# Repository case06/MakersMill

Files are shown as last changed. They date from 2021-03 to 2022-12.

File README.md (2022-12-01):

# MakersMill

[](
    https://opensourceecology.de)

This is the source repo for the "Maker's Mill"-Projekt on

https://wiki.opensourceecology.de/Maker%27s_Mill

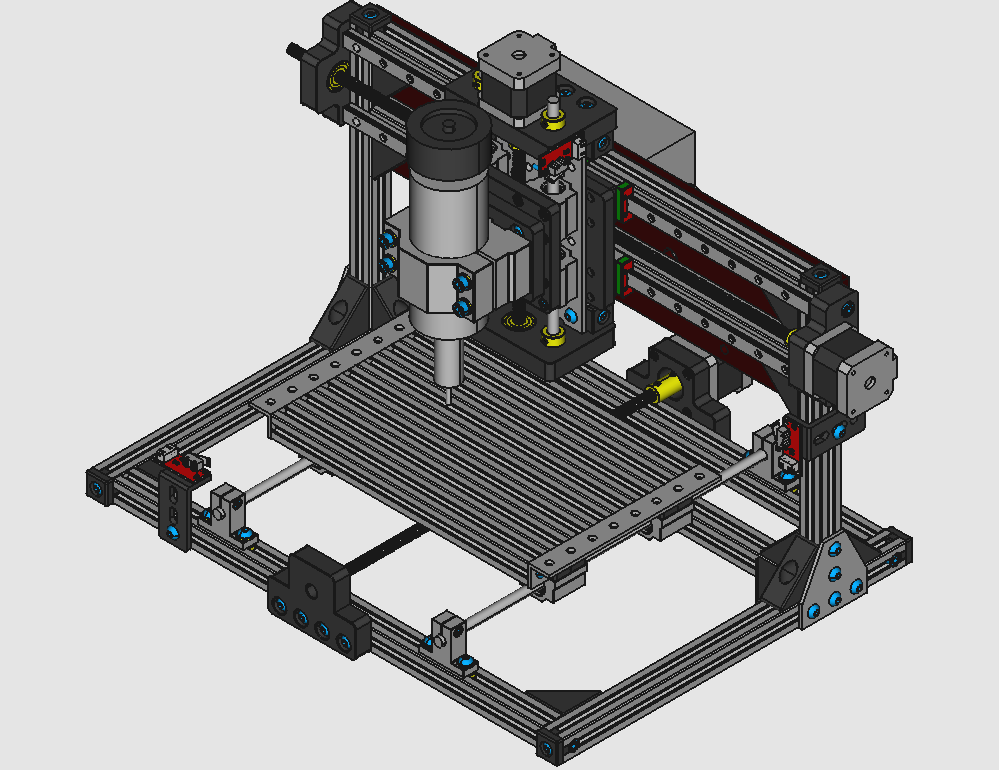
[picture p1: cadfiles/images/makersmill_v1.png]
Maker's Mill V.1.0
<p></p>

The projekt is based on the UniProKit 3D-part-library UPKlib V2.06, which is available at 

<a href="https://github.com/case06/upklib_v2"> https://github.com/case06/upklib_v2 </a>

The FreeCAD-sourcefiles of the current version can be viewed or modified with FreeCAD version 18 and 19

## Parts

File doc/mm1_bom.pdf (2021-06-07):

Seite 1

BOM Maker's Mill MM1 Desktop-Fräse V1.02, UniProKit UPKlib V2.06

Partname | PartNo. | Quantity Description | Pos | Supplier

Basis-Set
Tslot32con | 17092218 | 2 | T-Slot Con, 320x20x20mm | 1 | ML
Tslot40 | 17092208 | 5 | T-Slot Nut 6, 400x20x20mm | 2 | ML
Tslot24con | 17092217 | 2 | T-Slot Con, 240x20x20mm | 3 | ML
Tslot24 | 17092206 | 8 | T-Slot Nut 6, 240x20x20mm | 4 | ML
Tslot8 | 17092203 | 2 | T-Slot Nut 6, 80x20x20mm | 5 | ML
Flat16 | 17092239 | 2 | Flach, 160x40x4mm | 6 | ML
Angle16 | 17092228 | 2 | L-Profil, 160x20x20mm | 7 | ML
TCon | 17092302 | 2 | Flach, 60x60x4mm | 8 | ML
RAconnector | 17092313 | 18 | 90° Versteifungswinkel | 9 | ML
EndCap1d | 17092315 | 14 | Endkappe | 10 | ML
M6nutplate | 17092309 | 104 | für TSlot, Slot6, M6 | 11 | ML
M6x25cyl | 17092307 | 6 | 25mm, M6 DIN 7984 | 12 | ML, SP
M6x16 | 17092305 | 21 | 16mm, M6 ISO 7380 | 13 | ML, SP
M6x12 | 17092304 | 68 | 12mm, M6 ISO 7380 | 14 | ML, SP
M6x8 | 17092303 | 55 | 8mm, M6 ISO 7380 | 15 | ML, SP
M6wash | 17092310 | 12 | 6.4x12x1.6, DIN 125 | 16 | ML, SP
M6nut | 17092308 | 12 | 5.6x10mm, M6 DIN934 | 17 | ML, SP

Box-Set
3.5x16ws | 18081701 | 4 | WoodScrew | 18 | ML, SP

Set Lineardrive 1
M4nut | 19070613 | 12 | M4 Nut | 19 | ML, SP
M3x10cyl | 19070615 | 6 | 10mm, M3 ISO 4762 | 20 | ML, SP

Set Lineardrive 2
Mountplate3d | 21040802 | 1 | Motorplatte links | 21 | ML
Endplate1b | 19070624 | 0 | Loslager-Platte | 22 | ML
608ZZ_Ball_Bearing | 19082001 | 3 | Kugellager, 8mm innen | 23 | ML, SP
Carriageplate | 19070624 | 1 | Schlittenplatte | 24 | ML

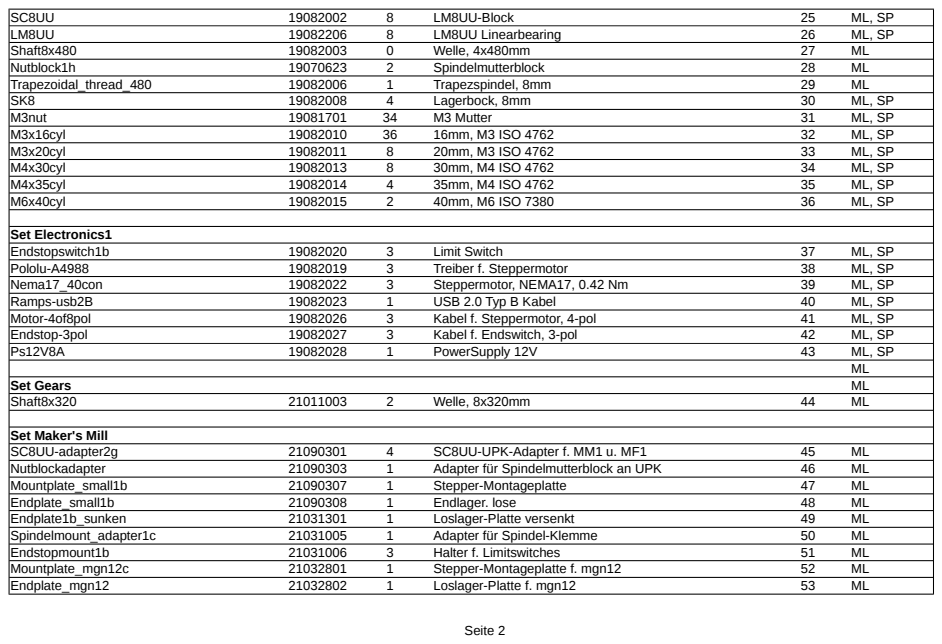
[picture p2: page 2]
Seite; LM8UU-Block; LM8UU Linearbearing; Shaft8x480; Welle, 4x480mm; Nutblock1h; Spindelmutterblock; Trapezoidal_thread_480; Trapezspindel, 8mm; Lagerbock, 8mm; M3nut; M3 Mutter; M3x16cyl; 16mm, M3 ISO 4762; M3x20cyl; 20mm, M3 ISO 4762; M4x30cyl; 30mm, M4 ISO 4762; M4x35cyl; 35mm, M4 ISO 4762; M6x40cyl; 40mm, M6 ISO 7380; Set Electronics1; Endstopswitch1b; Limit Switch; Pololu-A4988; Treiber f. Steppermotor; Nema17_40con; Steppermotor, NEMA17, 0.42 Nm; Ramps-usb2B; USB 2.0 Typ B Kabel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

Set Maker's Mill

Seite

3

Carriageplate-mgn12b | 21032810 | 1 | Schlittenplatte f. MGN12 | 54 | ML
M4x10cyl | 21090302 | 32 | 10mm, M4 ISO 4762 | 55 | ML, SP
M4x4lockscrew | 21090310 | 12 | M4x4 Madenschraube | 56 | ML, SP
M6x65cyl | 21031002 | 4 | 65mm, M6 ISO 7380 | 57 | ML, SP
M3x30cyl | 21032809 | 4 | 30 mm, M3 ISO 4762 | 58 | ML, SP
Trapezoidal-thread_320 | 21090306 | 1 | Trapezspindel, 8mm | 59 | ML
Trapezoidal_thread_160 | 20092406 | 1 | Trapezspindel, 160x8mm | 60 | ML
Trapezoidal_nut_AntiB | 21090304 | 6 | Trapezspindelmutter, 8mm, Antibacklash | 61 | ML, SP
Trapezoidal_nut_AntiB-spring | 21090305 | 6 | Feder f. Antibacklash-Trapezmutter 8mm | 62 | ML, SP
Rigidcoupler-5-8 | 21090309 | 3 | starre Wellenkupplung | 63 | ML, SP
Shaft8x210 | 20092405 | 2 | Welle, 210mm (Sondergröße) | 64 | ML
Adjustring8mm | 21031001 | 8 | Stellring | 65 | ML, SP
spindelmount52mm | 21031003 | 1 | Halter für 500W-Spindel, 52mm | 66 | ML, SP
spindel500w | 21031004 | 1 | 500W, 100V, 12000 rpm, 0.5 Nm, 1.08 Kg | 67 | ML, SP
Ks0288cncshield | 21031007 | 1 | Arduino kompatible Steuerung | 68 | ML, SP
ps500wspindel | 21031008 | 1 | PowerSupply 500w-Spindel | 69 | ML, SP
revctrl500wspindel | 21031009 | 1 | wth118-1a 2w 4k7 | 70 | ML, SP
Ctrlmount2g | 21031010 | 1 | Elektronik-Platte | 71 | ML
cabel220v | 21031011 | 1 | 220V AC-Kabel mit Stecker | 72 | ML, SP
cabel20awg | 21031012 | 1 | Kabel 0.75mm², awg20 | 73 | ML
terminalstrip1.5qmm | 21031013 | 1 | Lüsterklemme 1.5 mm², 16A | 74 | ML, SP
Mgn12h-block | 21032804 | 4 | carriage for MGN12H-rails | 75 | ML, SP
Mgn12h-rail-435 | 21032805 | 2 | 435mm MGN12H-rail | 76 | ML, SP
M3x8cyl | 21032807 | 32 | 8 mm, M3 ISO 4762 | 77 | ML, SP
Nutblock1i | 21032808 | 1 | Spindelmutterblock mit Senkmuttern | 78 | ML
revctrl-holder | 21040801 | 1 | Holder f. revctrl500wspindel | 79 | ML
Hammermutter-m3 | 21032803 | 32 | Hammermutter, M3, Slot6 | 80 | ML, SP
Limitflag | 21051901 | 1 | Y-endstop-marker | 81 | ML
cablehose | 21051902 | 1 | Kabelhülle 50cm u. 70cm | 82 | ML, SP
limitdistancer | 21051903 | 1 | Abstandhalter f. x-limitswitch | 83 | ML
Spannzangen-Set | - | 1 | ER11 Spannzangen m1-7 u. Halter | 84 | ML, SP

Seite 4

Std.-Part | SP | Standard-Part, widely available from several sources

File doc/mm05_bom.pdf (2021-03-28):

Seite 1

BOM Maker's Mill MM05 Desktop-Fräse, UniProKit UPKlib V2.05

Partname | PartNo. | | Description | Supplier

Basis-Set
Tslot32con | 17092218 | 2 | T-Slot Con, 320x20x20mm | ML
Tslot40 | 17092208 | 5 | T-Slot Nut 6, 400x20x20mm | ML
Tslot24con | 17092217 | 2 | T-Slot Con, 240x20x20mm | ML
Tslot24 | 17092206 | 8 | T-Slot Nut 6, 240x20x20mm | ML
Tslot8 | 17092203 | 2 | T-Slot Nut 6, 80x20x20mm | ML
Flat16 | 17092239 | 2 | Flach, 160x40x4mm | ML
Angle16 | 17092228 | 2 | L-Profil, 160x20x20mm | ML
TCon | 17092302 | 2 | Flach, 60x60x4mm | ML
RAconnector | 17092313 | 18 | 90° Versteifungswinkel | ML
EndCap1d | 17092315 | 28 | Endkappe | ML
M6nutplate | 17092309 | 114 | für TSlot, Slot6, M6 | ML
M6x25cyl | 17092307 | 6 | 25mm, M6 DIN 7984 | ML, SP
M6x16 | 17092305 | 24 | 16mm, M6 ISO 7380 | ML, SP
M6x12 | 17092304 | 68 | 12mm, M6 ISO 7380 | ML, SP
M6x8 | 17092303 | 58 | 8mm, M6 ISO 7380 | ML, SP
M6wash | 17092310 | 20 | 6.4x12x1.6, DIN 125 | ML, SP
M6nut | 17092308 | 12 | 5.6x10mm, M6 DIN934 | ML, SP

Box-Set
3.5x16ws | 18081701 | 4 | WoodScrew | ML, SP

Set Lineardrive 1
M4nut | 19070613 | 12 | M4 Nut | ML, SP
M3x10cyl | 19070615 | 6 | 10mm, M3 ISO 4762 | ML, SP

Set Lineardrive 2
Mountplate3b | 19070623 | 2 | Motorplatte links | ML
Endplate1b | 19070624 | 1 | Loslager-Platte | ML
608ZZ_Ball_Bearing | 19082001 | 3 | Kugellager, 8mm innen | ML, SP
Carriageplate | 19070624 | 2 | Schlittenplatte | ML

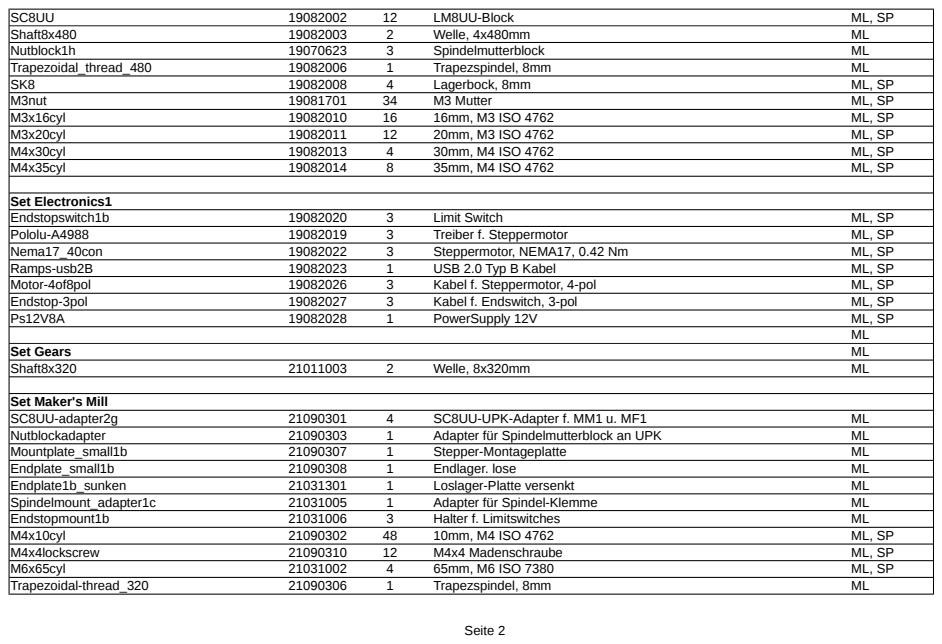
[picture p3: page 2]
Seite; LM8UU-Block; Shaft8x480; Welle, 4x480mm; Nutblock1h; Spindelmutterblock; Trapezoidal_thread_480; Trapezspindel, 8mm; Lagerbock, 8mm; M3nut; M3 Mutter; M3x16cyl; 16mm, M3 ISO 4762; M3x20cyl; 20mm, M3 ISO 4762; M4x30cyl; 30mm, M4 ISO 4762; M4x35cyl; 35mm, M4 ISO 4762; Set Electronics1; Endstopswitch1b; Limit Switch; Pololu-A4988; Treiber f. Steppermotor; Nema17_40con; Steppermotor, NEMA17, 0.42 Nm; Ramps-usb2B; USB 2.0 Typ B Kabel; Motor-4of8pol; Kabel f. Steppermotor, 4-pol; Endstop-3pol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

Set Maker's Mill

Seite 3

Trapezoidal_thread_160 | 20092406 | 1 | Trapezspindel, 160x8mm | ML
Trapezoidal_nut_AntiB | 21090304 | 3 | Trapezspindelmutter, 8mm, Antibacklash | ML, SP
Trapezoidal_nut_AntiB-spring | 21090305 | 3 | Feder f. Antibacklash-Trapezmutter 8mm | ML, SP
Rigidcoupler-5-8 | 21090309 | 3 | starre Wellenkupplung | ML, SP
Shaft8x210 | 20092405 | 2 | Welle, 210mm (Sondergröße) | ML
Adjustring8mm | 21031001 | 16 | Stellring | ML, SP
spindelmount52mm | 21031003 | 1 | Halter für 500W-Spindel, 52mm | ML, SP
spindel500w | 21031004 | 1 | 500W, 100V, 12000 rpm, 0.5 Nm, 1.08 Kg | ML, SP
Ks0288cncshield | 21031007 | 1 | Arduino kompatible Steuerung | ML, SP
ps500wspindel | 21031008 | 1 | PowerSupply 500w-Spindel | ML, SP
revctrl500wspindel | 21031009 | 1 | wth118-1a 2w 4k7 | ML, SP
Ctrlmount2f | 21031010 | 1 | Elektronik-Platte | ML
cabel220v | 21031011 | 1 | 220V AC-Kabel mit Stecker | ML, SP
cabel20awg | 21031012 | 1 | Kabel 0.75mm², awg20 | ML
terminalstrip1.5qmm | 21031013 | 1 | Lüsterklemme 1.5 mm², 16A | ML, SP
Std.-Part | SP | Standard-Part, widely available from several sources

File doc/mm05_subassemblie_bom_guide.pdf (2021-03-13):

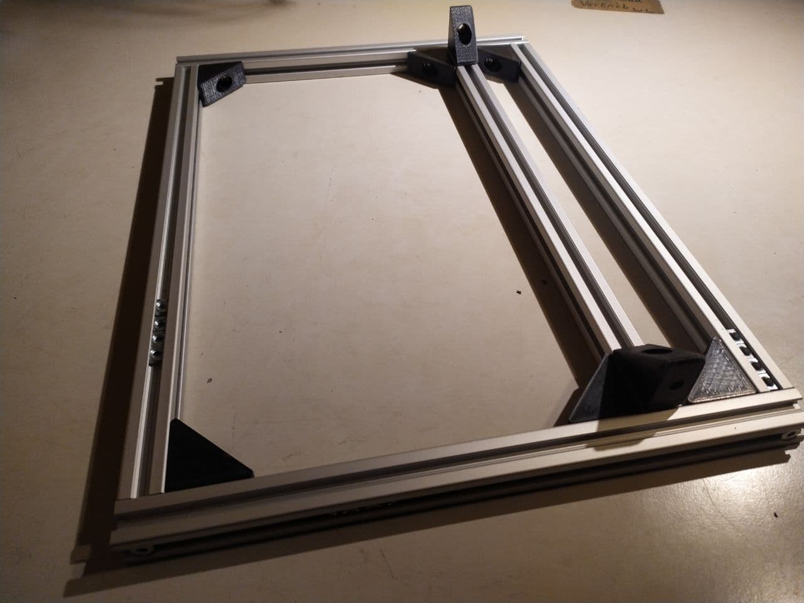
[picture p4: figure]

Seite 1

Subassemblie-BOM Maker's Mill MM05 Desktop-Fräse, UniProKit UPKlib V2.05

Rahmen

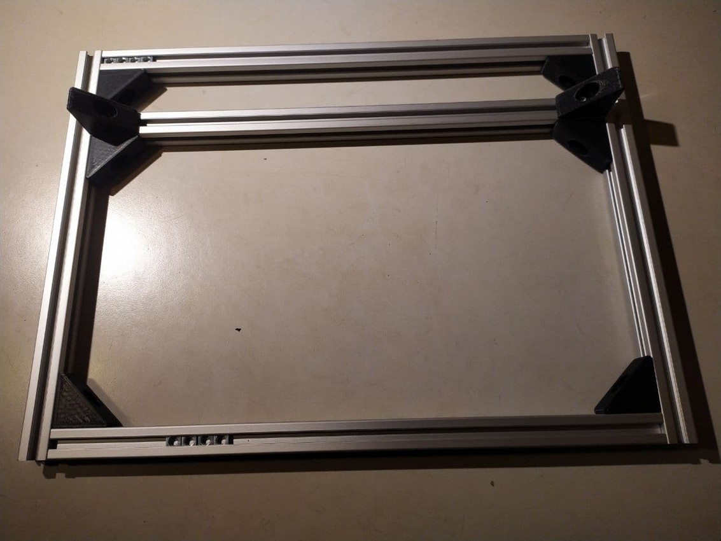
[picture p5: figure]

Y-Base
Name | Bauteil/A.-Nr. | Stück | Funktion
Tslot32con | 17092218 | 2 | T-Slot Con, 320x20x20mm
Tslot40 | 17092208 | 3 | T-Slot Nut 6, 400x20x20mm
RAconnector | 17092313 | 8 | 90° Versteifungswinkel
M6nutplate | 17092309 | 37 | für TSlot, Slot6, M6
M6x25cyl | 17092307 | 4 | 25mm, M6 DIN 7984
M6x12 | 17092304 | 14 | 12mm, M6 ISO 7380
M6x8 | 17092303 | 8 | 8mm, M6 ISO 7380
EndCap1d | 17092315 | 8 | Endkappe

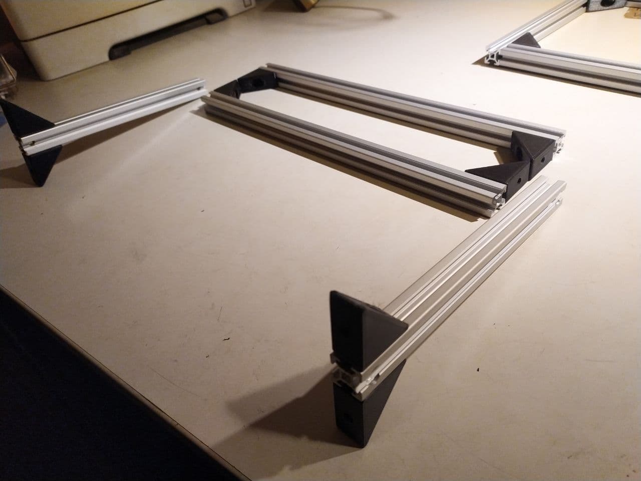
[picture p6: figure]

Seite 2

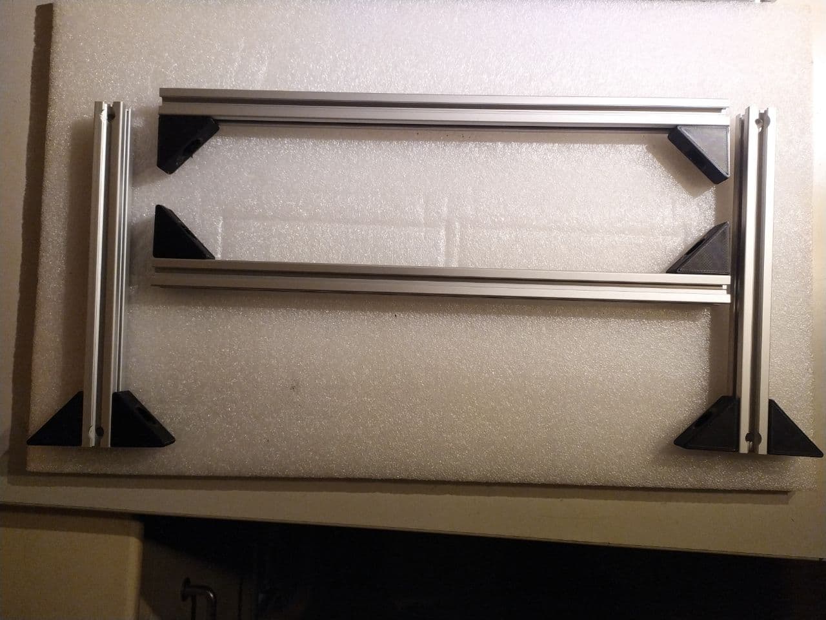
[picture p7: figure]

X-Gantry
Name | Bauteil/A.-Nr. | Stück | Funktion
Tslot40 | 17092208 | 2 | T-Slot Nut 6, 400x20x20mm
Tslot24con | 17092217 | 2 | T-Slot Con, 240x20x20mm
RAconnector | 17092313 | 10 | 90° Versteifungswinkel
M6nutplate | 17092309 | 39 | für TSlot, Slot6, M6
M6x25cyl | 17092307 | 2 | 25mm, M6 DIN 7984
M6x12 | 17092304 | 22 | 12mm, M6 ISO 7380
EndCap1d | 17092315 | 6 | Endkappe
M6x8 | 17092303 | 10 | 8mm, M6 ISO 7380
TCon | 17092302 | 2 | Flach, 60x60x4mm
M6x8 | 17092303 | 2 | 8mm, M6 ISO 7380
EndCap1d | 17092315 | 2 | Endkappe

Seite 3

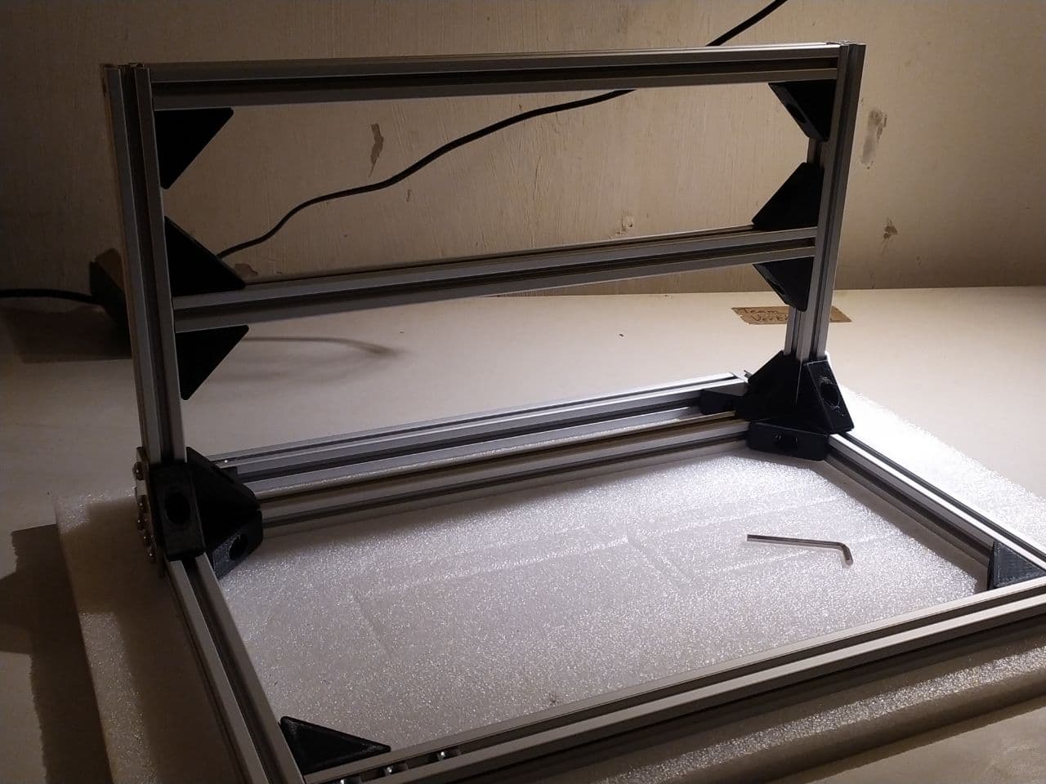
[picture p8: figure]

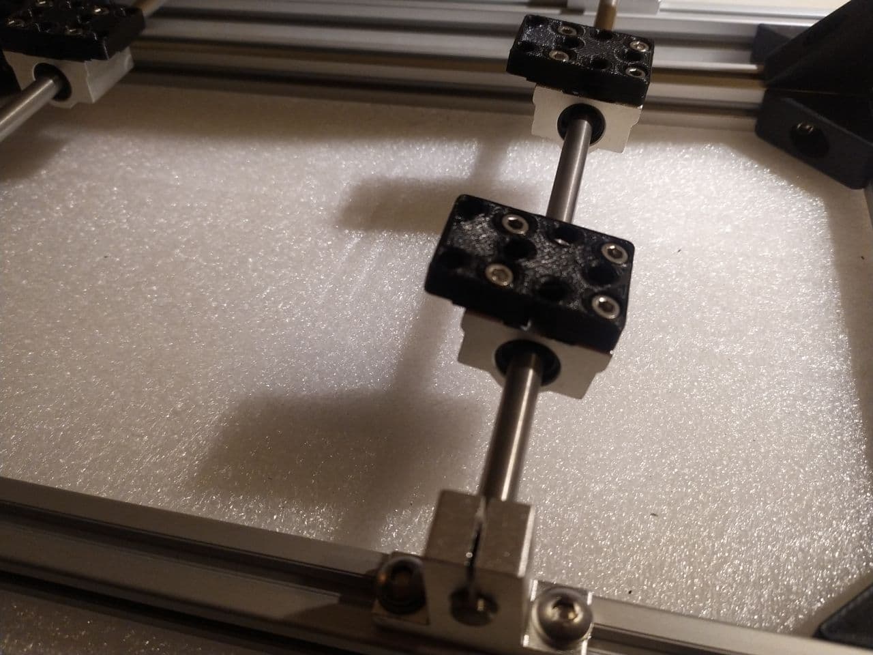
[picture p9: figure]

Seite 4

Y-Achse


Y-Achse
Name | Bauteil/A.-Nr. | Stück | Funktion
Shaft8x320 | 21011003 | 2 | Welle, 8x320mm
SK8 | 19082008 | 4 | Lagerbock, 8mm
SC8UU | 19082002 | 4 | LM8UU-Block
M6x12 | 17092304 | 12 | 12mm, M6 ISO 7380
M6wash | 17092310 | 4 | 6.4x12x1.6, DIN 125
Tslot24 | 17092206 | 8 | T-Slot Nut 6, 240x20x20mm
Angle16 | 17092228 | 2 | L-Profil, 160x20x20mm
M6x8 | 17092303 | 16 | 8mm, M6 ISO 7380
SC8UU-adapter2g | 21090301 | 4 | SC8UU-UPK-Adapter f. MM1 u. MF1
M6nutplate | 17092309 | 18 | für TSlot, Slot6, M6
M4x10cyl | 21090302 | 16 | 10mm, M4 ISO 4762
M6x12 | 17092304 | 8 | 12mm, M6 ISO 7380


Seite 5

Seite 6

Y-Trapezgewinde-Antrieb

Y-Trapezgewinde-Antrieb
Name | Bauteil/A.-Nr. | Stück | Funktion
Nutblock1h | 19070623 | 1 | Spindelmutterblock
M3x20cyl | 19082011 | 4 | 20mm, M3 ISO 4762
M3nut | 19081701 | 4 | M3 Mutter
M4x35cyl | 19082014 | 4 | 35mm, M4 ISO 4762
M4nut | 19070613 | 4 | M4 Nut
Nutblockadapter | 21090303 | 1 | Adapter für Spindelmutterblock an UPK
Trapezoidal_nut_AntiB | 21090304 | 1 | Trapezspindelmutter, 8mm, Antibacklash
Trapezoidal_nut_AntiB-spring | 21090305 | 1 | Feder f. Antibacklash-Trapezmutter 8mm
Trapezoidal-thread_320 | 21090306 | 1 | Trapezspindel, 8mm
Mountplate_small1b | 21090307 | 1 | Stepper-Montageplatte
608ZZ_Ball_Bearing | 19082001 | 1 | Kugellager, 8mm innen
M6x16 | 17092305 | 8 | 16mm, M6 ISO 7380
Endplate_small1b | 21090308 | 1 | Endlager. lose
Nema17_40con | 19082022 | 1 | Steppermotor, NEMA17, 0.42 Nm
M3x16cyl | 19082010 | 4 | 16mm, M3 ISO 4762
Rigidcoupler-5-8 | 21090309 | 1 | starre Wellenkupplung
M4x4lockscrew | 21090310 | 4 | M4x4 Madenschraube


Seite 7


Seite 8

Seite 9

X-Achse

Name | Bauteil/A.-Nr. | Stück | Funktion

X-Achse

Mountplate3b | 19070623 | 1 | Motorplatte links
Endplate1b | 19070624 | 1 | Loslager-Platte
608ZZ_Ball_Bearing | 19082001 | 1 | Kugellager
M3x16cyl | 19082010 | 4 | 16mm, M3 ISO 4762
Nema17_40con | 19082022 | 1 | Steppermotor, NEMA17, 0.42 Nm
Rigidcoupler-5-8 | 21090309 | 1 | starre Wellenkupplung
M4x4lockscrew | 21090310 | 4 | M4x4 Madenschraube
Trapezoidal_thread_480 | 19082006 | 1 | Trapezspindel, 8mm
Shaft8x480 | 19082003 | 2 | Welle, 4x480mm, vgl. auch Gears-Set
Adjustring8mm | 21031001 | 8 | Stellring
Nutblock1h | 19070623 | 1 | Spindelmutterblock
Trapezoidal_nut_AntiB | 21090304 | 1 | Trapezspindelmutter, 8mm, Antibacklash
Trapezoidal_nut_AntiB-spring | 21090305 | 1 | Feder f. Antibacklash-Trapezmutter 8mm
Carriageplate | 19070624 | 1 | Schlittenplatte
M6nut | 17092308 | 4 | 5.6x10mm, M6 DIN934
SC8UU | 19082002 | 4 | LM8UU-Block
M3x20cyl | 19082011 | 4 | 20mm, M3 ISO 4762
M3nut | 19081701 | 4 | M3 Mutter
M4x35cyl | 19082014 | 4 | 35mm, M4 ISO 4762
M4nut | 19070613 | 4 | M4 Nut
M4x10cyl | 21090302 | 16 | 10mm, M4 ISO 4762
M6wash | 17092310 | 8 | 6.4x12x1.6, DIN 125
M6x16 | 17092305 | 8 | 16mm, M6 ISO 7380
M6x8 | 17092303 | 8 | 8mm, M6 ISO 7380
EndCap1d | 17092315 | 8 | Endkappe


Seite 10

Seite 11


Seite 12

Z-Achse

Name | Bauteil/A.-Nr. | Stück | Funktion
Z-Achse
Mountplate3b | 19070623 | 1 | Motorplatte links
Endplate1b_sunken | 21031301 | 1 | Loslager-Platte versenkt
608ZZ_Ball_Bearing | 19082001 | 1 | Kugellager
M6wash | 17092310 | 8 | 6.4x12x1.6, DIN 125
M6x16 | 17092305 | 8 | 16mm, M6 ISO 7380
M6nutplate | 17092309 | 16 | für TSlot, Slot6, M6
Flat16 | 17092239 | 2 | Flach, 160x40x4mm
Tslot8 | 17092203 | 2 | T-Slot Nut 6, 80x20x20mm
M6x8 | 17092303 | 12 | 8mm, M6 ISO 7380
EndCap1d | 17092315 | 4 | Endkappe
Carriageplate | 19070624 | 1 | Schlittenplatte
M6nut | 17092308 | 4 | 5.6x10mm, M6 DIN934
SC8UU | 19082002 | 4 | LM8UU-Block
M4x10cyl | 21090302 | 16 | 10mm, M4 ISO 4762
Shaft8x210 | 20092405 | 2 | Welle, 210mm (Sondergröße)
Adjustring8mm | 21031001 | 8 | Stellring
M3x16cyl | 19082010 | 4 | 16mm, M3 ISO 4762
Nema17_40con | 19082022 | 1 | Steppermotor, NEMA17, 0.42 Nm
Trapezoidal_nut_AntiB | 21090304 | 1 | Trapezspindelmutter, 8mm, Antibacklash
Trapezoidal_nut_AntiB-spring | 21090305 | 1 | Feder f. Antibacklash-Trapezmutter 8mm
Trapezoidal_thread_160 | 20092406 | 1 | Trapezspindel, 160x8mm
Nutblock1h | 19070623 | 1 | Spindelmutterblock
M3x20cyl | 19082011 | 4 | 20mm, M3 ISO 4762
M3nut | 19081701 | 4 | M3 Mutter
M4x30cyl | 19082013 | 4 | 30mm, M4 ISO 4762
M4nut | 19070613 | 4 | M4 Nut
M4x4lockscrew | 21090310 | 4 | M4x4 Madenschraube
Rigidcoupler-5-8 | 21090309 | 1 | starre Wellenkupplung


Seite 13


Seite 14


Seite 15


Seite 16

Name | Bauteil/A.-Nr. | Stück | Funktion

Spindel

Spindelmount_adapter1c | 21031005 | 1 | Adapter für Spindel-Klemme
M6nut | 17092308 | 4 | 5.6x10mm, M6 DIN934
M6x12 | 17092304 | 8 | 12mm, M6 ISO 7380
M6x65cyl | 21031002 | 4 | 65mm, M6 ISO 7380
spindelmount52mm | 21031003 | 1 | Halter für 500W-Spindel, 52mm
spindel500w | 21031004 | 1 | 500W, 100V, 12000 rpm, 0.5 Nm, 1.08 Kg



Seite 17


Seite 18

Steuerung

Name | Bauteil/A.-Nr. | Stück | Funktion

Elektronik

Endstopmount1b | 21031006 | 3 | Halter f. Limitswitches
Endstopswitch1b | 19082020 | 3 | Limit Switch
M6x8 | 17092303 | 2 | 8mm, M6 ISO 7380
3.5x16ws | 18081701 | 4 | WoodScrew
M3x10cyl | 19070615 | 4 | 10mm, M3 ISO 4762
M3nut | 19081701 | 8 | M3 Mutter
Ctrlmount2f | 21031010 | 1 | Elektronik-Platte
M6x12 | 17092304 | 4 | 12mm, M6 ISO 7380
M6nutplate | 17092309 | 4 | für TSlot, Slot6, M6
Ks0288cncshield | 21031007 | 1 | Arduino kompatible Steuerung
M3nut | 19081701 | 12 | M3 Mutter
M3x16cyl | 19082010 | 4 | 16mm, M3 ISO 4762
Pololu-A4988 | 19082019 | 3 | Treiber f. Steppermotor
Motor-4of8pol | 19082026 | 3 | Kabel f. Steppermotor, 4-pol
Endstop-3pol | 19082027 | 3 | Kabel f. Endswitch, 3-pol
Ramps-usb2B | 19082023 | 1 | USB 2.0 Typ B Kabel
ps500wspindel | 21031008 | 1 | PowerSupply 500w-Spindel
M3x10cyl | 19070615 | 2 | 10mm, M3 ISO 4762
M3nut | 19081701 | 2 | M3 Mutter
revctrl500wspindel | 21031009 | 1 | wth118-1a 2w 4k7
cabel220v | 21031011 | 1 | 220V AC-Kabel mit Stecker
cabel20awg | 21031012 | 1 | Kabel 0.75mm², awg20
terminalstrip1.5qmm | 21031013 | 1 | Lüsterklemme 1.5 mm², 16A
Ps12V8A | 19082028 | 1 | PowerSupply 12V


Seite 19


Seite 20

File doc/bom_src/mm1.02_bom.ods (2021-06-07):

BOM Maker's Mill MM1 Desktop-Fräse V1.02, UniProKit UPKlib V2.06
Partname |  |  | PartNo. | Quantity | Description | Pos | Supplier
Basis-Set
Tslot32con |  |  | 17092218 | 2 | T-Slot Con, 320x20x20mm | 1 | ML
Tslot40 |  |  | 17092208 | 5 | T-Slot Nut 6, 400x20x20mm | 2 | ML
Tslot24con |  |  | 17092217 | 2 | T-Slot Con, 240x20x20mm | 3 | ML
Tslot24 |  |  | 17092206 | 8 | T-Slot Nut 6, 240x20x20mm | 4 | ML
Tslot8 |  |  | 17092203 | 2 | T-Slot Nut 6, 80x20x20mm | 5 | ML
Flat16 |  |  | 17092239 | 2 | Flach, 160x40x4mm | 6 | ML
Angle16 |  |  | 17092228 | 2 | L-Profil, 160x20x20mm | 7 | ML
TCon |  |  | 17092302 | 2 | Flach, 60x60x4mm | 8 | ML
RAconnector |  |  | 17092313 | 18 | 90° Versteifungswinkel | 9 | ML
EndCap1d |  |  | 17092315 | 14 | Endkappe | 10 | ML
M6nutplate |  |  | 17092309 | 104 | für TSlot, Slot6, M6 | 11 | ML
M6x25cyl |  |  | 17092307 | 6 | 25mm, M6 DIN 7984 | 12 | ML, SP
M6x16 |  |  | 17092305 | 21 | 16mm, M6 ISO 7380 | 13 | ML, SP
M6x12 |  |  | 17092304 | 68 | 12mm, M6 ISO 7380 | 14 | ML, SP
M6x8 |  |  | 17092303 | 55 | 8mm, M6 ISO 7380 | 15 | ML, SP
M6wash |  |  | 17092310 | 12 | 6.4x12x1.6, DIN 125 | 16 | ML, SP
M6nut |  |  | 17092308 | 12 | 5.6x10mm, M6 DIN934 | 17 | ML, SP
Box-Set
3.5x16ws |  |  | 18081701 | 4 | WoodScrew | 18 | ML, SP
Set Lineardrive 1
M4nut |  |  | 19070613 | 12 | M4 Nut | 19 | ML, SP
M3x10cyl |  |  | 19070615 | 6 | 10mm, M3 ISO 4762 | 20 | ML, SP
Set Lineardrive 2
Mountplate3d |  |  | 21040802 | 1 | Motorplatte links | 21 | ML
Endplate1b |  |  | 19070624 | 0 | Loslager-Platte | 22 | ML
608ZZ_Ball_Bearing |  |  | 19082001 | 3 | Kugellager, 8mm innen | 23 | ML, SP
Carriageplate |  |  | 19070624 | 1 | Schlittenplatte | 24 | ML
SC8UU |  |  | 19082002 | 8 | LM8UU-Block | 25 | ML, SP
LM8UU |  |  | 19082206 | 8 | LM8UU Linearbearing | 26 | ML, SP
Shaft8x480 |  |  | 19082003 | 0 | Welle, 4x480mm | 27 | ML
Nutblock1h |  |  | 19070623 | 2 | Spindelmutterblock | 28 | ML
Trapezoidal_thread_480 |  |  | 19082006 | 1 | Trapezspindel, 8mm | 29 | ML
SK8 |  |  | 19082008 | 4 | Lagerbock, 8mm | 30 | ML, SP
M3nut |  |  | 19081701 | 34 | M3 Mutter | 31 | ML, SP
M3x16cyl |  |  | 19082010 | 36 | 16mm, M3 ISO 4762 | 32 | ML, SP
M3x20cyl |  |  | 19082011 | 8 | 20mm, M3 ISO 4762 | 33 | ML, SP
M4x30cyl |  |  | 19082013 | 8 | 30mm, M4 ISO 4762 | 34 | ML, SP
M4x35cyl |  |  | 19082014 | 4 | 35mm, M4 ISO 4762 | 35 | ML, SP
M6x40cyl |  |  | 19082015 | 2 | 40mm, M6 ISO 7380 | 36 | ML, SP
Set Electronics1
Endstopswitch1b |  |  | 19082020 | 3 | Limit Switch | 37 | ML, SP
Pololu-A4988 |  |  | 19082019 | 3 | Treiber f. Steppermotor | 38 | ML, SP
Nema17_40con |  |  | 19082022 | 3 | Steppermotor, NEMA17, 0.42 Nm | 39 | ML, SP
Ramps-usb2B |  |  | 19082023 | 1 | USB 2.0 Typ B Kabel | 40 | ML, SP
Motor-4of8pol |  |  | 19082026 | 3 | Kabel f. Steppermotor, 4-pol | 41 | ML, SP
Endstop-3pol |  |  | 19082027 | 3 | Kabel f. Endswitch, 3-pol | 42 | ML, SP
Ps12V8A |  |  | 19082028 | 1 | PowerSupply 12V | 43 | ML, SP
 |  |  |  |  |  |  | ML
Set Gears |  |  |  |  |  |  | ML
Shaft8x320 |  |  | 21011003 | 2 | Welle, 8x320mm | 44 | ML
Set Maker's Mill
SC8UU-adapter2g |  |  | 21090301 | 4 | SC8UU-UPK-Adapter f. MM1 u. MF1 | 45 | ML
Nutblockadapter |  |  | 21090303 | 1 | Adapter für Spindelmutterblock an UPK | 46 | ML
Mountplate_small1b |  |  | 21090307 | 1 | Stepper-Montageplatte | 47 | ML
Endplate_small1b |  |  | 21090308 | 1 | Endlager. lose | 48 | ML
Endplate1b_sunken |  |  | 21031301 | 1 | Loslager-Platte versenkt | 49 | ML
Spindelmount_adapter1c |  |  | 21031005 | 1 | Adapter für Spindel-Klemme | 50 | ML
Endstopmount1b |  |  | 21031006 | 3 | Halter f. Limitswitches | 51 | ML
Mountplate_mgn12c |  |  | 21032801 | 1 | Stepper-Montageplatte f. mgn12 | 52 | ML
Endplate_mgn12 |  |  | 21032802 | 1 | Loslager-Platte f. mgn12 | 53 | ML
Carriageplate-mgn12b |  |  | 21032810 | 1 | Schlittenplatte f. MGN12 | 54 | ML
M4x10cyl |  |  | 21090302 | 32 | 10mm, M4 ISO 4762 | 55 | ML, SP
M4x4lockscrew |  |  | 21090310 | 12 | M4x4 Madenschraube | 56 | ML, SP
M6x65cyl |  |  | 21031002 | 4 | 65mm, M6 ISO 7380 | 57 | ML, SP
M3x30cyl |  |  | 21032809 | 4 | 30 mm, M3 ISO 4762 | 58 | ML, SP
Trapezoidal-thread_320 |  |  | 21090306 | 1 | Trapezspindel, 8mm | 59 | ML
Trapezoidal_thread_160 |  |  | 20092406 | 1 | Trapezspindel, 160x8mm | 60 | ML
Trapezoidal_nut_AntiB |  |  | 21090304 | 6 | Trapezspindelmutter, 8mm, Antibacklash | 61 | ML, SP
Trapezoidal_nut_AntiB-spring |  |  | 21090305 | 6 | Feder f. Antibacklash-Trapezmutter 8mm | 62 | ML, SP
Rigidcoupler-5-8 |  |  | 21090309 | 3 | starre Wellenkupplung | 63 | ML, SP
Shaft8x210 |  |  | 20092405 | 2 | Welle, 210mm (Sondergröße) | 64 | ML
Adjustring8mm |  |  | 21031001 | 8 | Stellring | 65 | ML, SP
spindelmount52mm |  |  | 21031003 | 1 | Halter für 500W-Spindel, 52mm | 66 | ML, SP
spindel500w |  |  | 21031004 | 1 | 500W, 100V, 12000 rpm, 0.5 Nm, 1.08 Kg | 67 | ML, SP
Ks0288cncshield |  |  | 21031007 | 1 | Arduino kompatible Steuerung | 68 | ML, SP
ps500wspindel |  |  | 21031008 | 1 | PowerSupply 500w-Spindel | 69 | ML, SP
revctrl500wspindel |  |  | 21031009 | 1 | wth118-1a 2w 4k7 | 70 | ML, SP
Ctrlmount2g |  |  | 21031010 | 1 | Elektronik-Platte | 71 | ML
cabel220v |  |  | 21031011 | 1 | 220V AC-Kabel mit Stecker | 72 | ML, SP
cabel20awg |  |  | 21031012 | 1 | Kabel 0.75mm², awg20 | 73 | ML
terminalstrip1.5qmm |  |  | 21031013 | 1 | Lüsterklemme 1.5 mm², 16A | 74 | ML, SP
Mgn12h-block |  |  | 21032804 | 4 | carriage for MGN12H-rails | 75 | ML, SP
Mgn12h-rail-435 |  |  | 21032805 | 2 | 435mm MGN12H-rail | 76 | ML, SP
M3x8cyl |  |  | 21032807 | 32 | 8 mm, M3 ISO 4762 | 77 | ML, SP
Nutblock1i |  |  | 21032808 | 1 | Spindelmutterblock mit Senkmuttern | 78 | ML
revctrl-holder |  |  | 21040801 | 1 | Holder f. revctrl500wspindel | 79 | ML
Hammermutter-m3 |  |  | 21032803 | 32 | Hammermutter, M3, Slot6 | 80 | ML, SP
Limitflag |  |  | 21051901 | 1 | Y-endstop-marker | 81 | ML
cablehose |  |  | 21051902 | 1 | Kabelhülle 50cm u. 70cm | 82 | ML, SP
limitdistancer |  |  | 21051903 | 1 | Abstandhalter f. x-limitswitch | 83 | ML
Spannzangen-Set |  |  | - | 1 | ER11 Spannzangen m1-7 u. Halter | 84 | ML, SP
Supplier | Id | URL
Std.-Part | SP | Standard-Part, widely available from several sources
Makers-Lab | ML | http:makers-lab.de

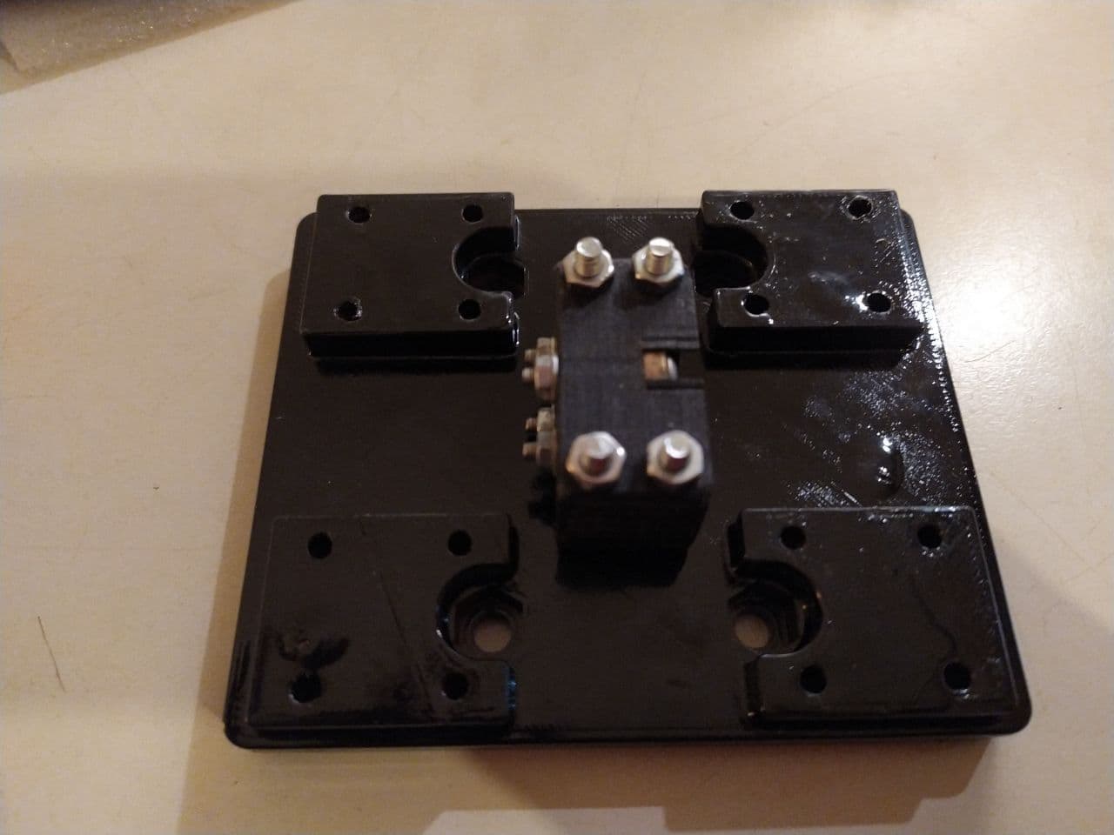
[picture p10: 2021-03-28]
doc/bom_src/images/mgn12-carriage2.jpg

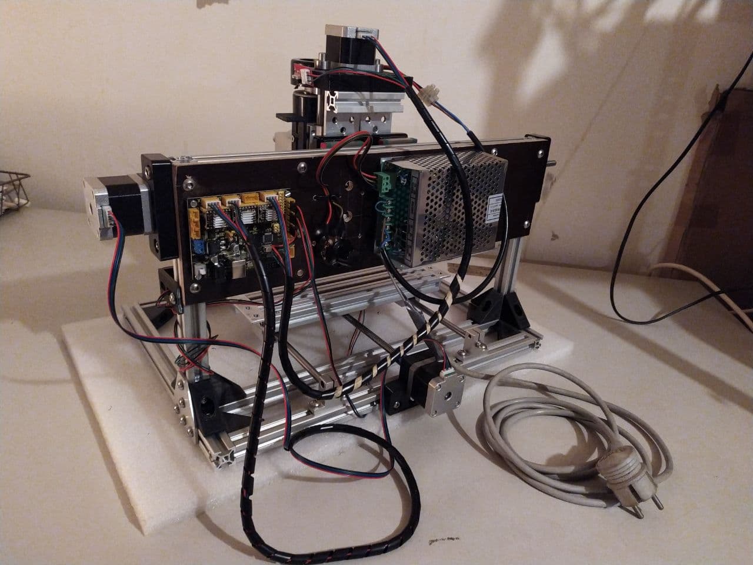
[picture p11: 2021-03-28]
doc/bom_src/images/mm_v.1.0_back.jpg

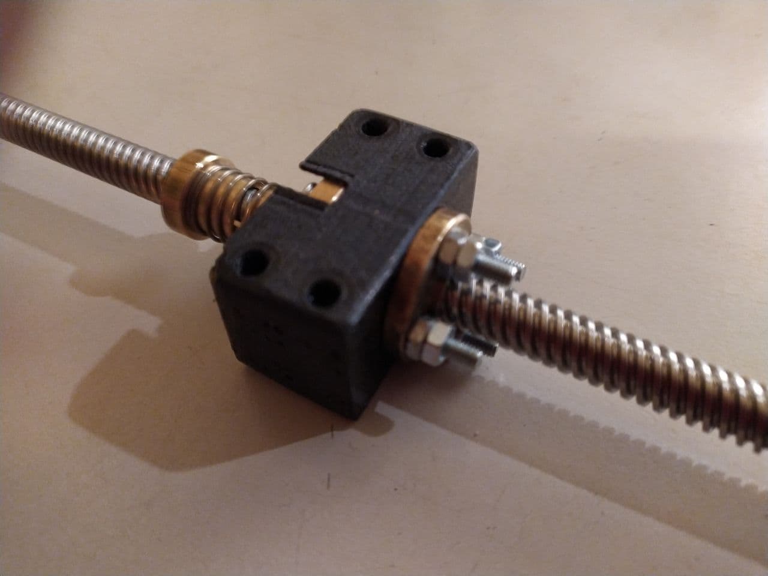
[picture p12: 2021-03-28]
doc/bom_src/images/mgn12-Spindelmutterblock1.jpg

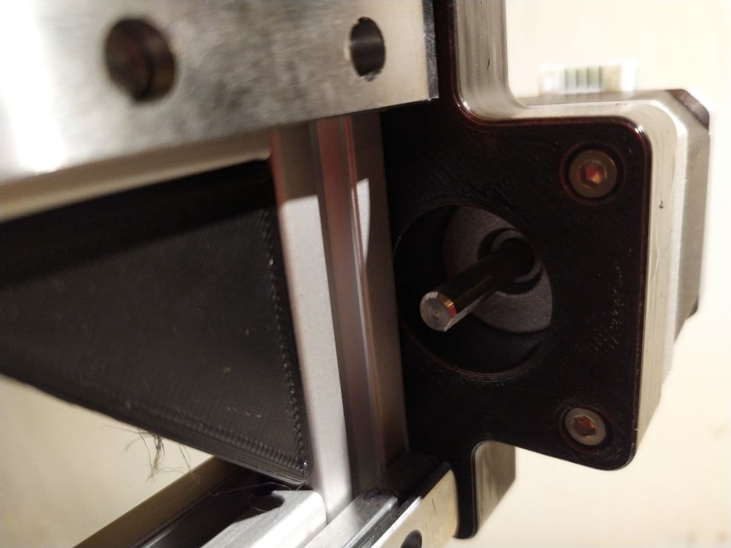
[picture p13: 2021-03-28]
doc/bom_src/images/mgn12-stepper-mountplate1_ass.jpg

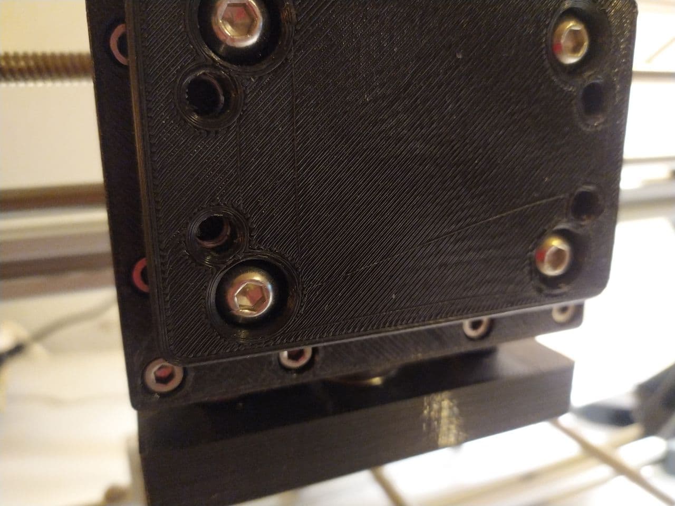
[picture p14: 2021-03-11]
doc/bom_src/images/z-spindelmount_adapter.jpg

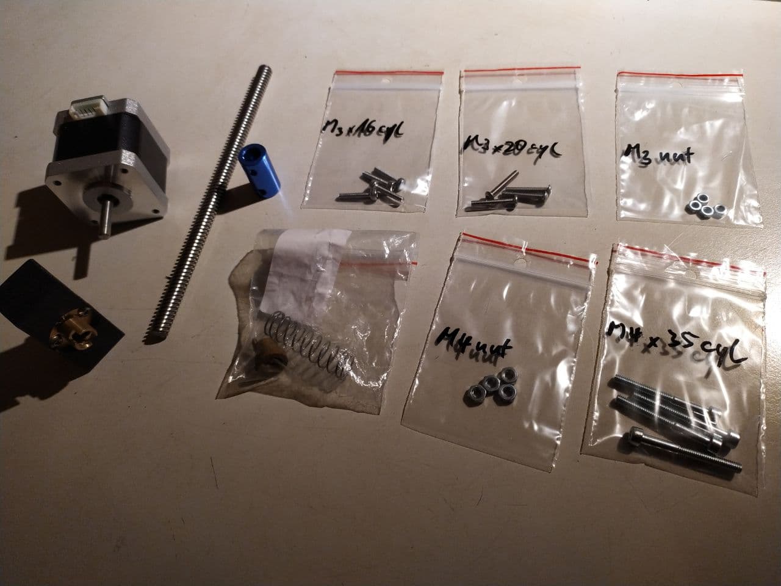
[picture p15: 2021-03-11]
doc/bom_src/images/z-achse-kit_antrieb.jpg

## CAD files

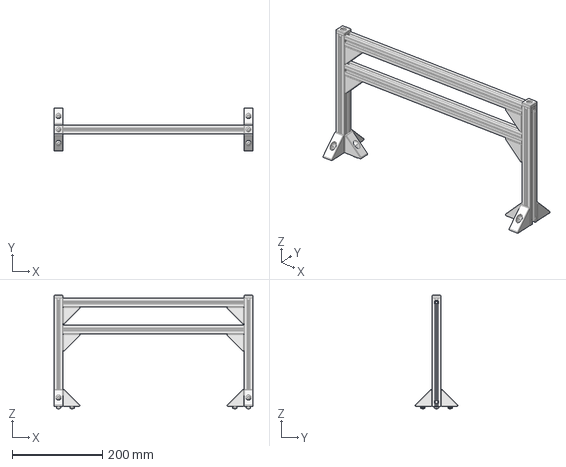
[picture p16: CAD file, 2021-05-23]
cadfiles/assemblies/z-frame_v1.FCStd
440.0 x 94.3 x 251.0 mm

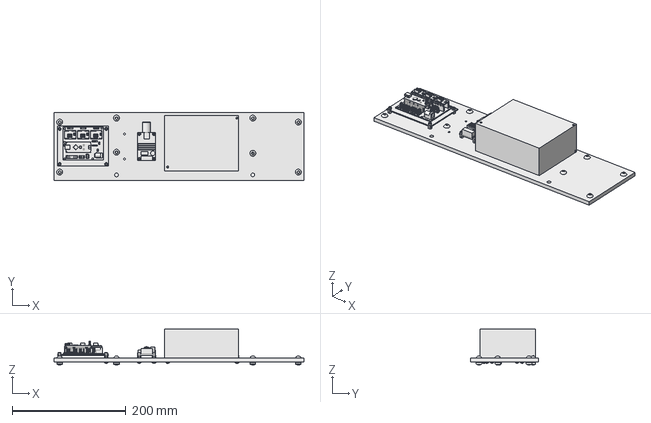
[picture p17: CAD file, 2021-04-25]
cadfiles/assemblies/ctrl-board_v1.FCStd
440.0 x 120.0 x 63.0 mm

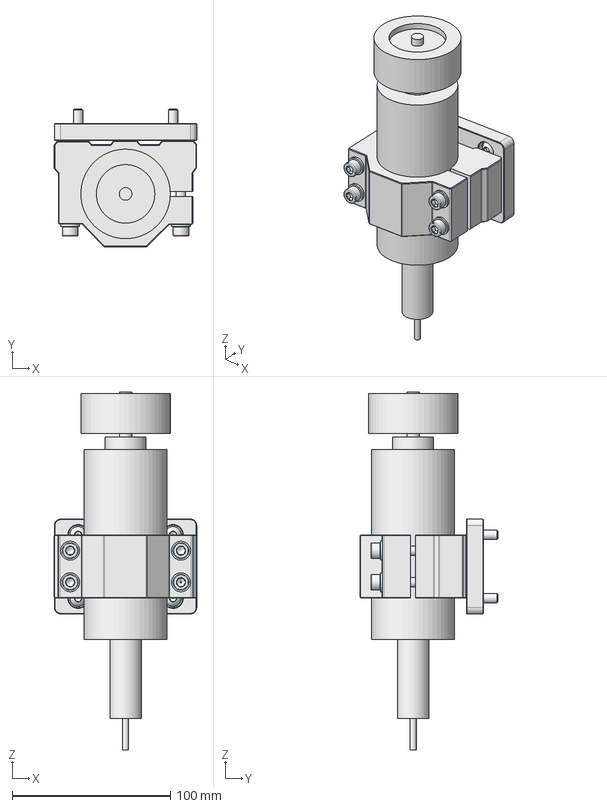
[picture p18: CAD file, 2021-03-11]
cadfiles/assemblies/spindel.FCStd
90.1 x 87.1 x 226.3 mm

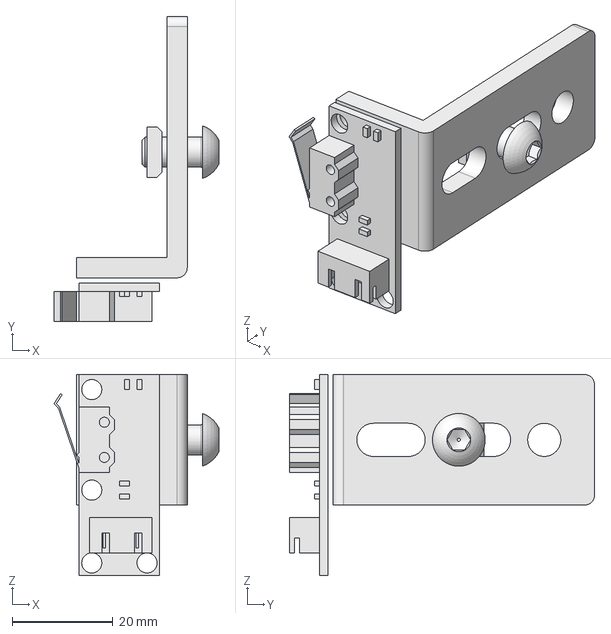
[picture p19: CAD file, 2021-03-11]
cadfiles/assemblies/x-switch.FCStd
32.8 x 60.7 x 40.0 mm

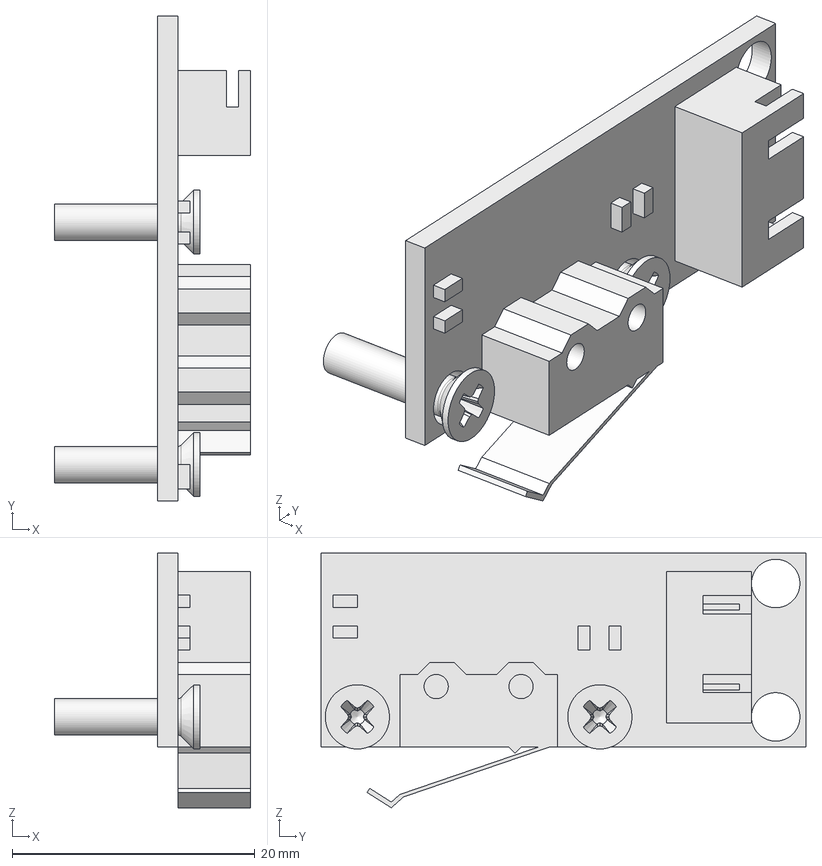
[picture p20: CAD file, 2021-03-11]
cadfiles/assemblies/z-switch.FCStd
16.2 x 40.0 x 21.0 mm

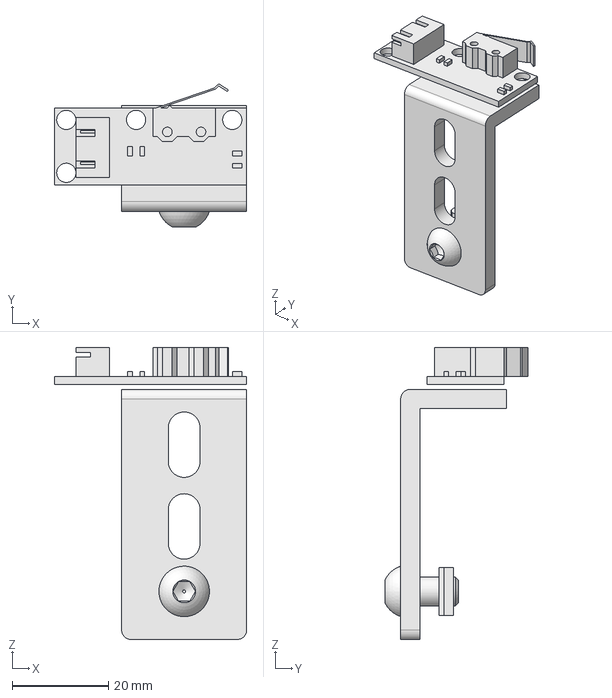
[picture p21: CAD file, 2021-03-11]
cadfiles/assemblies/y-switch.FCStd
40.0 x 29.8 x 60.7 mm

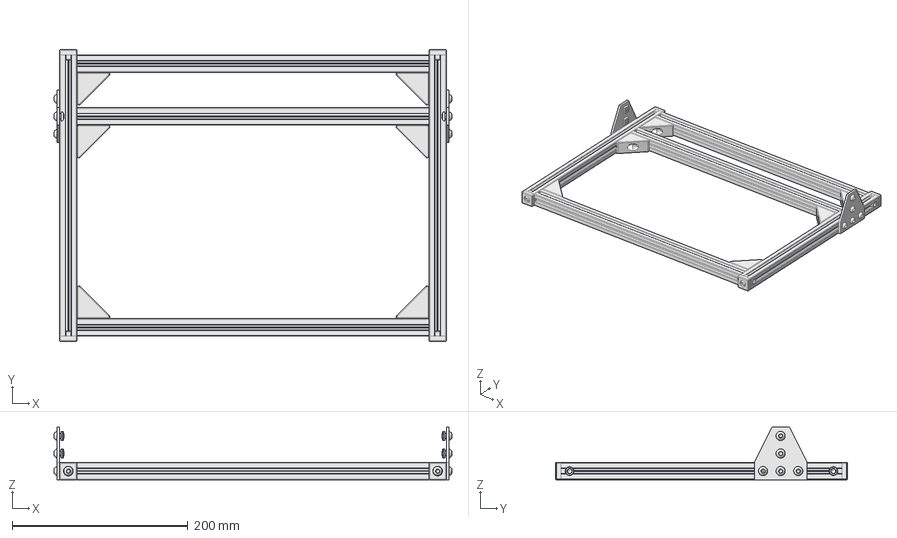
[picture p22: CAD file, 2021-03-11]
cadfiles/assemblies/xy-frame.FCStd
452.6 x 332.0 x 60.0 mm

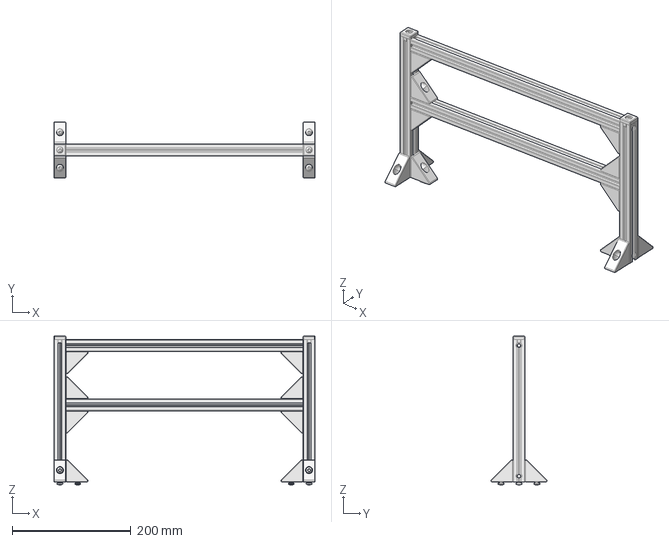
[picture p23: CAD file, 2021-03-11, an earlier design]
cadfiles/assemblies/z-frame.FCStd
440.0 x 94.3 x 251.0 mm

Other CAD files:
cadfiles/assemblies/ctrl-board.FCStd

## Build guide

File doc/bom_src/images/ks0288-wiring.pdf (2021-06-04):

Stepper connections
X | Y | Z

Limit-Switches

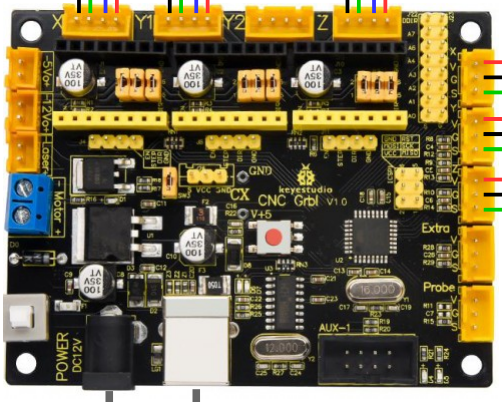
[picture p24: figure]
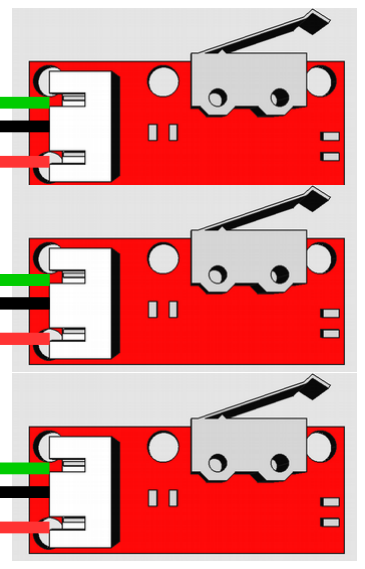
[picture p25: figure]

X

Y

Z

12V
DC

USB

Wiring diagram for UniProKit Maker's Mill MM1 with GRBL-CNC-Shield KS0288

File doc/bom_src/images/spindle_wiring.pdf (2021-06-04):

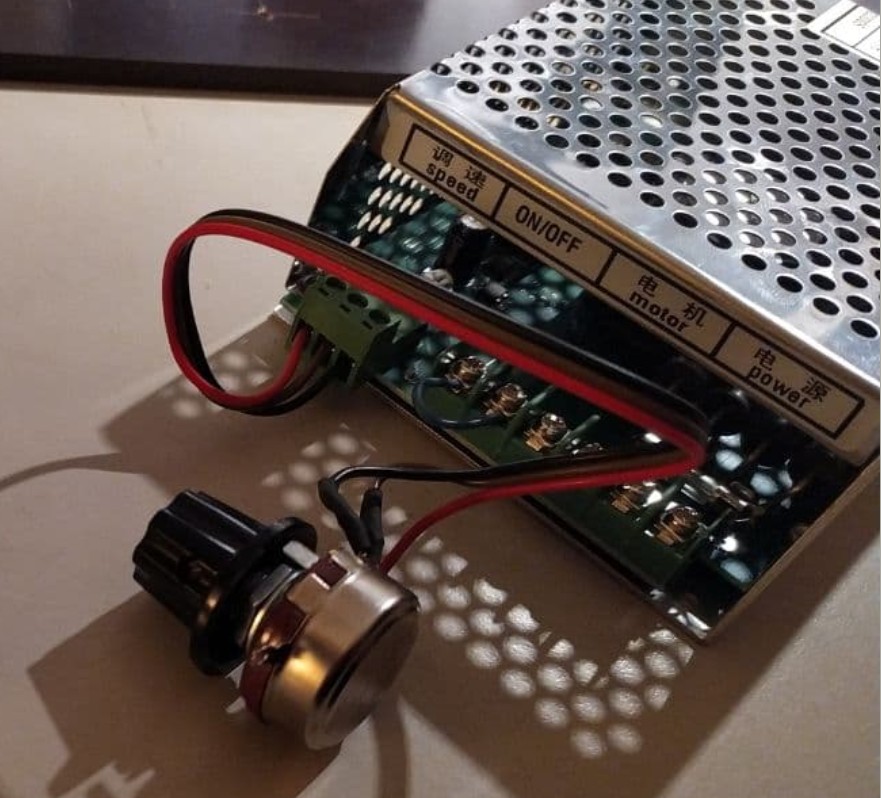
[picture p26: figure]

Knob

Wiring diagram for UniProKit Maker's Mill MM1 with 500 W Spindle and 230V Powersupply

Speed

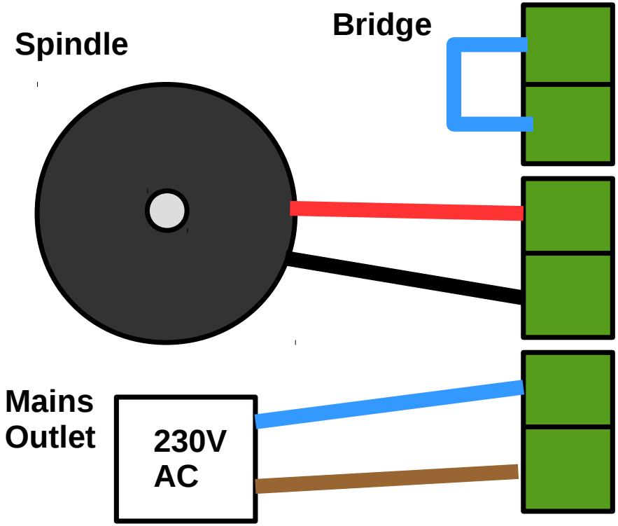
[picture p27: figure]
Spindle; Mains Outlet; Bridge

On / Off

Spindle
Motor

Power

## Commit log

2021-03-11 doc files added
    [mm05_subassemblie_bom_guide.ods]
2021-03-11 added sub-assemblies freecad files
    [ctrl-board.FCStd, spindel.FCStd, x-switch.FCStd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]
2021-03-11 added sub-assemblies image files
2021-03-13 added condensed bom
    [mm05_bom.ods]
2021-03-13 minor changes
    [mm05_subassemblie_bom_guide.ods]
2021-03-13 added supplier
    [mm05_bom.ods]
2021-03-13 set version
    [mm05_subassemblie_bom_guide.ods]
2021-03-28 added mgn12-x-achse for Version 1.0
    [mm05_bom.ods, mm1_bom.ods]
2021-03-28 added lm8uu
    [mm1_bom.ods]
2021-03-28 minor typo
    [mm1_bom.ods]
2021-04-08 added revctrl-holder
    [mm1_bom.ods]
2021-04-08 added mountplate3d
    [mm1_bom.ods]
2021-04-25 added new ctrlmnt2g version
    [ctrl-board_v1.FCStd, mm1_bom.ods]
2021-04-26 added the new V1/mgn12 version of x-axis
2021-05-22 corrected numbers of m6nutplates and endcaps in subassembly-bom in the assemblies y-base, x-gantry, x-achse, z-achse and spindel
    [mm1.02_bom.ods, mm1_bom.ods]
2021-05-22 removed backs folder
    [mm1_bom.ods]
2021-05-23 added corrected z-frame / gantry version
    [mm1.02_bom.ods, z-frame_v1.FCStd]
2021-06-04 added wiring diagram
2021-06-07 added wiring diagrams
2021-06-07 added screws and nuts for switches
    [mm1.02_bom.ods]
2021-06-21 changed release numbers
    [mm1_bom.ods]
